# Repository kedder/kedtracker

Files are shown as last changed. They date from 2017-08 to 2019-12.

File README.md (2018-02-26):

# Ked Tracker - Open Glider Network tracker hardware

Based on design by glidernet.org project: http://wiki.glidernet.org/ogn-tracker-diy.

It is a small airborn avionic device that periodically transmits aircraft
position. Signal is picked up by ground-based receivers and published on Open
Glider Network, so that aircraft position can be found on  various aircraft
tracking systems, like http://glidertracker.de/ or
https://www.flightradar24.com/. It is also received by other OGN tracker
devices in the vicinity and can be used to improve pilot' situation awareness.
See http://wiki.glidernet.org/ for more information.

Ked Tracker is designed using [KiCad](http://kicad-pcb.org/) electronic schematic and PCB design software.

## Features

* Can be powered from onboard 12V power supply (or any 9-24V power
  supply for that matter).

* Standard NMEA output.

* Uses FLARM NMEA sentences to report detected nearby aircrafts for
  interoperability with existing hardware and software.

* Communication via standard IGC RJ45 socket.
  Allows to re-use existing equipment like FLARM viewers or cables.

* Communication via USB interface. Device is visible as virtual COM port
  when connected to a computer. Requires no special cables other then standerd
  micro-USB cable. Device can also be powered by 5V from USB interface.

* Communication via Bluetooth. For hassle-free wireless connection with
  phone or tablet.

* Barometric sensor onboard for more precise altitude measurement.

* Slot for SD-card. Currently for logging device activity. Firmware for IGC
  flight logger is pending.

* Beeper to provide sound feedback for important events.

## Schematics

Current schematics can be also downloaded in
[PDF format](hardware/render/kedtracker.pdf?raw=true).

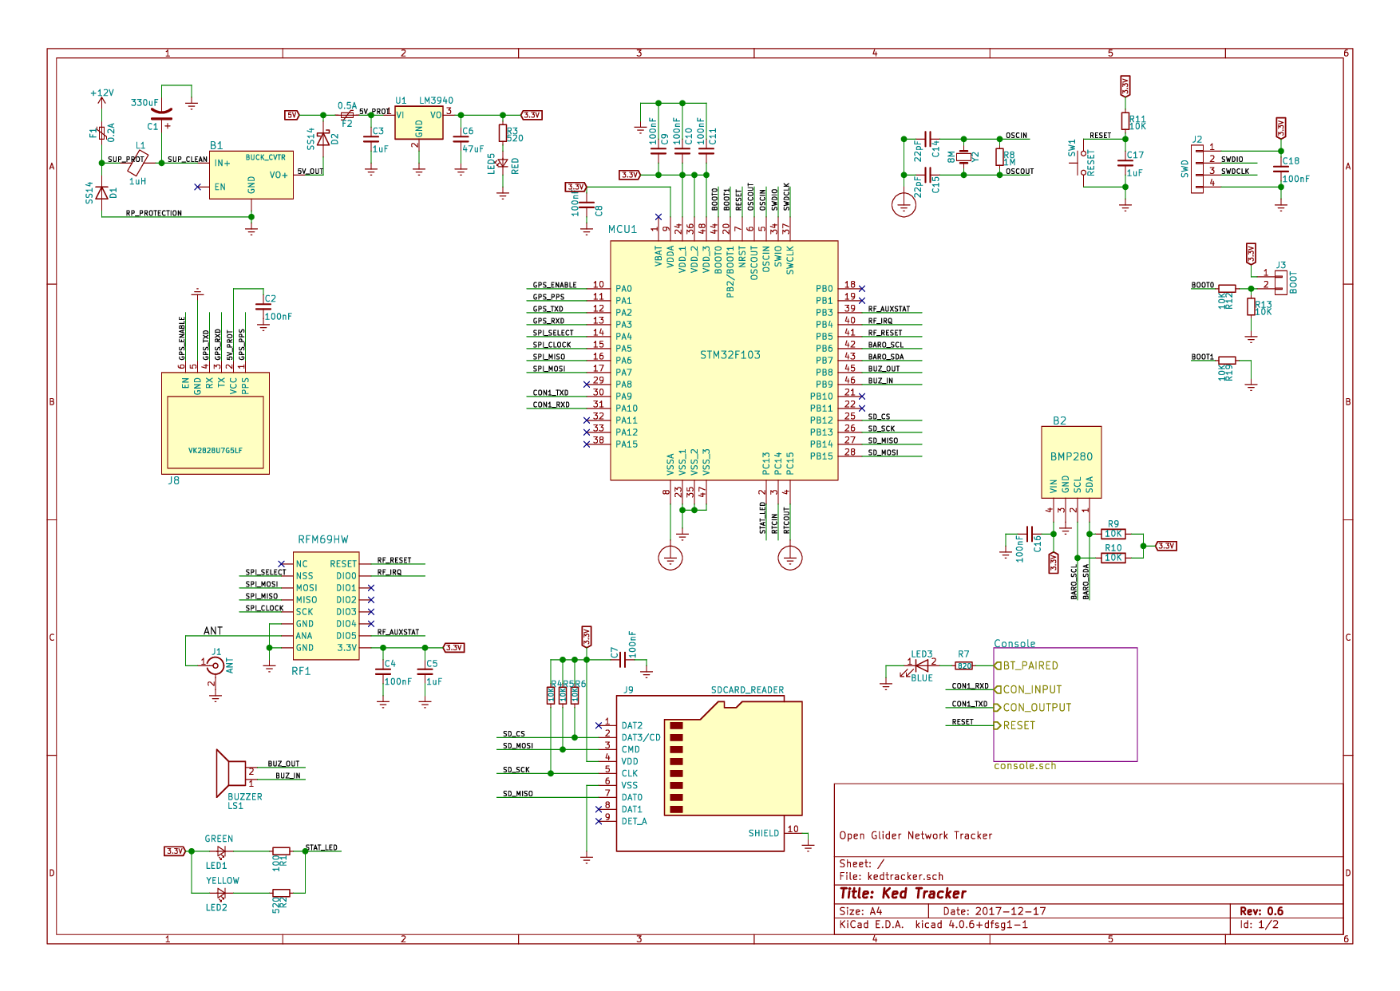
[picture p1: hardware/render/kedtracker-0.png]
Schematic Page 1

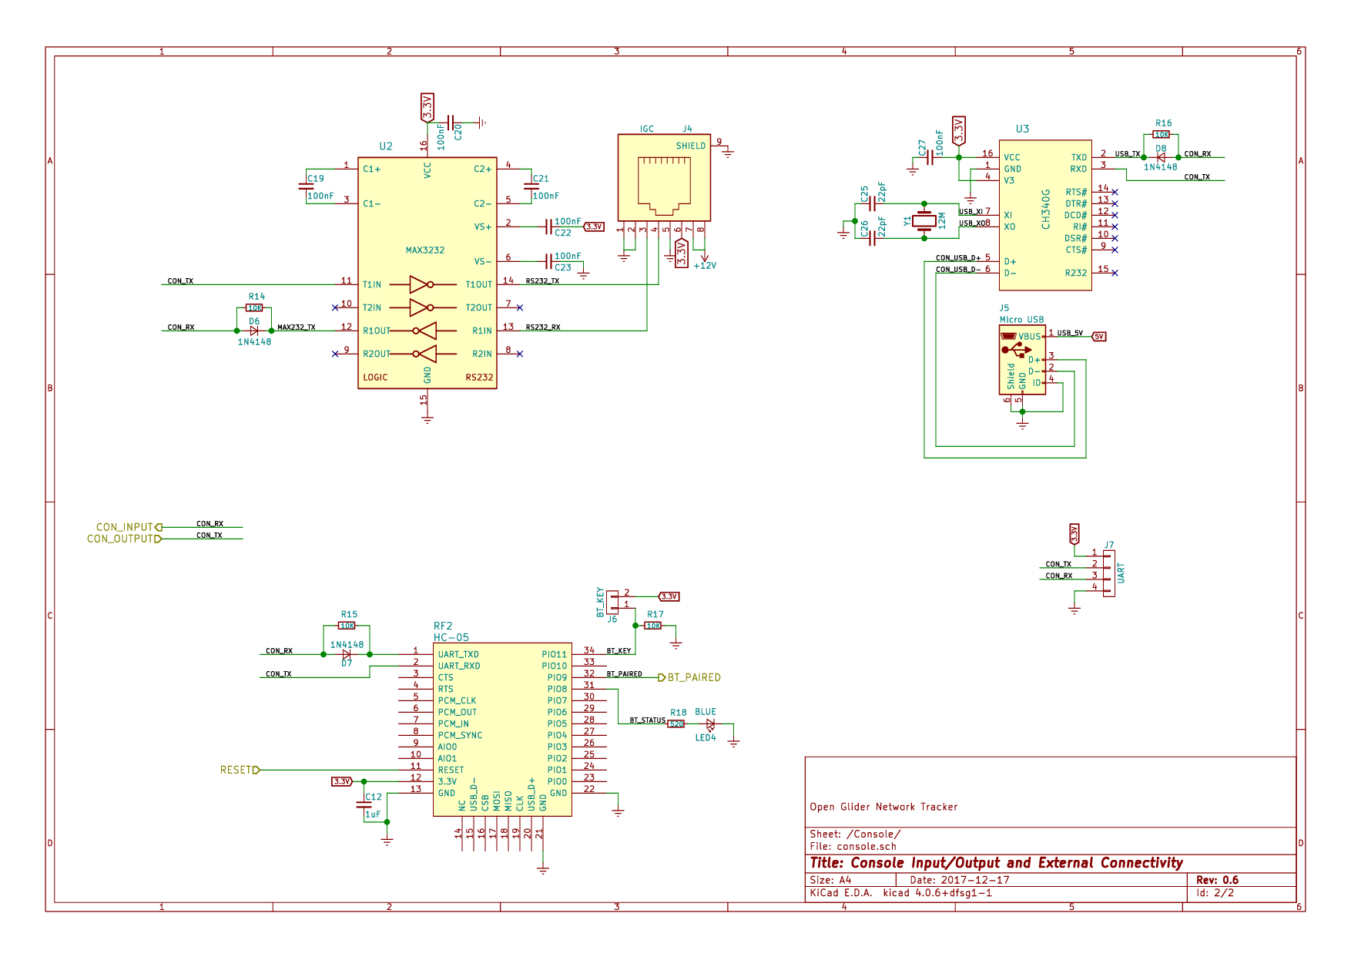
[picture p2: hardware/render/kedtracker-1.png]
Schematic Page 2


## Setting Up Development Environment

You will need to install additional packages for development. Packages for
ubuntu are specified here; other operating systems might have similar
requirements.

### Building Firmware and Flashing MCU

```
sudo apt install gcc-arm-none-eabi openocd picocom
sudo add-user `whoami` plugdev
sudo add-user `whoami` dialout
```

### Developing Hardware

```
sudo apt install kicad
```

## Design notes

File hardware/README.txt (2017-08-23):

OGN Tracker Hardware

Notes:

To create laser printer templates plot:

  Front Layer: Mirrored
  Bottom Layer: Non-mirrored

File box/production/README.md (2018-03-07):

# Labels for produced boxes

This directory is automatically populated with labels for enclosures.

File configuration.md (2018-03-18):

# Configuring

# Tracker settings

## Tracker
Tracker is configured using $POGNS NMEA sentence

```
$POGNS,ACFTT,ADDRT,ADDR,RFT,TXPW,FQCORR,
```

Where:

  * `ACFTT` -- [0..15] aircraft-type: 1=glider, 2=towa plane, 3=helicopter, ...
  * `ADDRT` -- [0..3] addr-type: 1=ICAO, 2=FLARM, 3=OGN
  * `ADDR` -- [HHHHHH] Address (ID): 6 hex digits, 24-bit
  * `RFT` -- [0..1] RFM69HW (up to +20dBm) or W (up to +13dBm)
  * `TXPW` -- [dBm] Tx power, from -10 to 20
  * `FQCORR` -- [Hz] Tx/Rx frequency correction

Examples:

Set high transmission power:
```
$POGNS,TxPower=20
```

## Bluetooth Dongles

### HC-05

HC-05 requires "Key" pin (34) to be brought high in order to enter "AT mode".
Once in at mode, open serial terminal on 38400 baud rate and execute these
commands (each command should end with `CR` `LF`:

```
    AT
    AT+VERSION?
    AT+NAME=Ked Tracker XXXXXX
    AT+UART=115200,0,0
```

Default PIN is `1234`.

### HC-06

HC-06 is by default configured to read on 9600 baud rate. Connect it to via
USB-TTL cable and issue the following commands (no CR or LF at the end):

```
    AT
    AT+VERSION
    AT+NAMEKEDBTX
    AT+BAUD8
```

Default PIN is `1234`.

### HC-10 Bluetooth LE

HC-06 is by default configured to read on 9600 baud rate. It accepts commands
with CR+LF endings. To configure, use these commands:

```
    AT+VERSION
    AT+NAMEKEDBTX
    AT+BAUD8
```

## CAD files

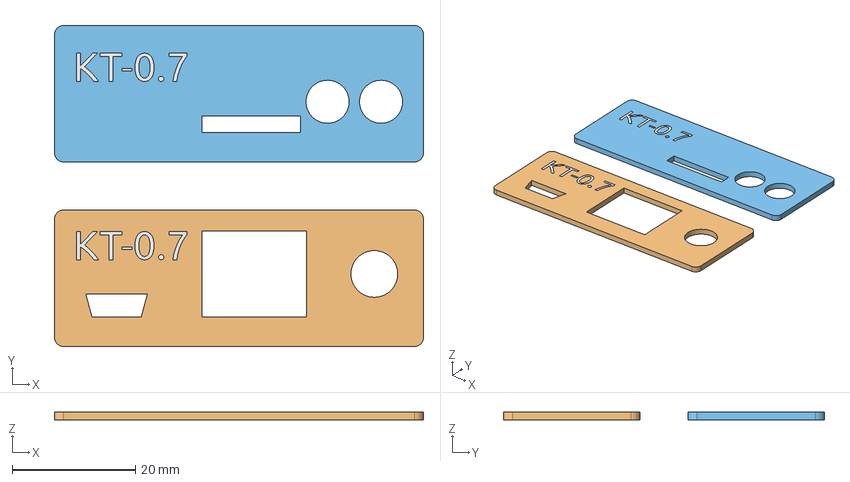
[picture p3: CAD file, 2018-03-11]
box/sideplates-0.7.fcstd
60.0 x 52.2 x 1.30 mm
Version-Front
Version-Back
Cut Back
Cut Front

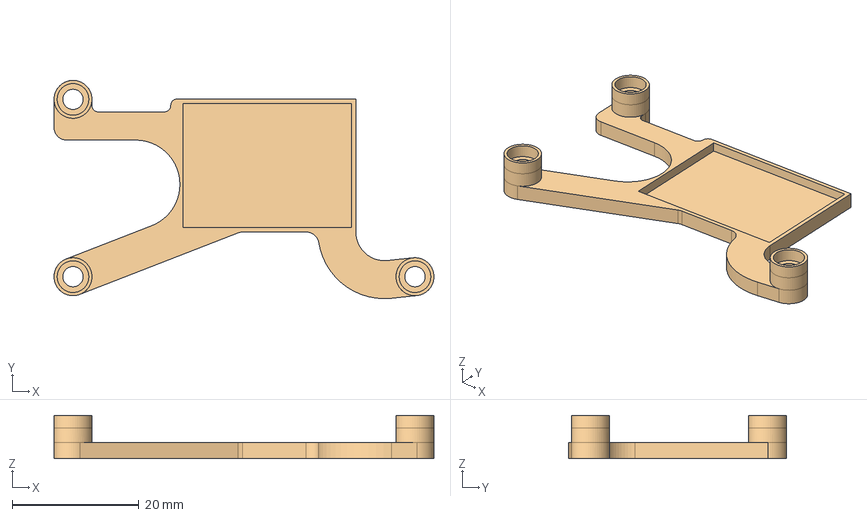
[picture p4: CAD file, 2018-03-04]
box/gpsframe2.fcstd
60.0 x 34.5 x 6.80 mm

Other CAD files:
box/sideplates-0.6.fcstd

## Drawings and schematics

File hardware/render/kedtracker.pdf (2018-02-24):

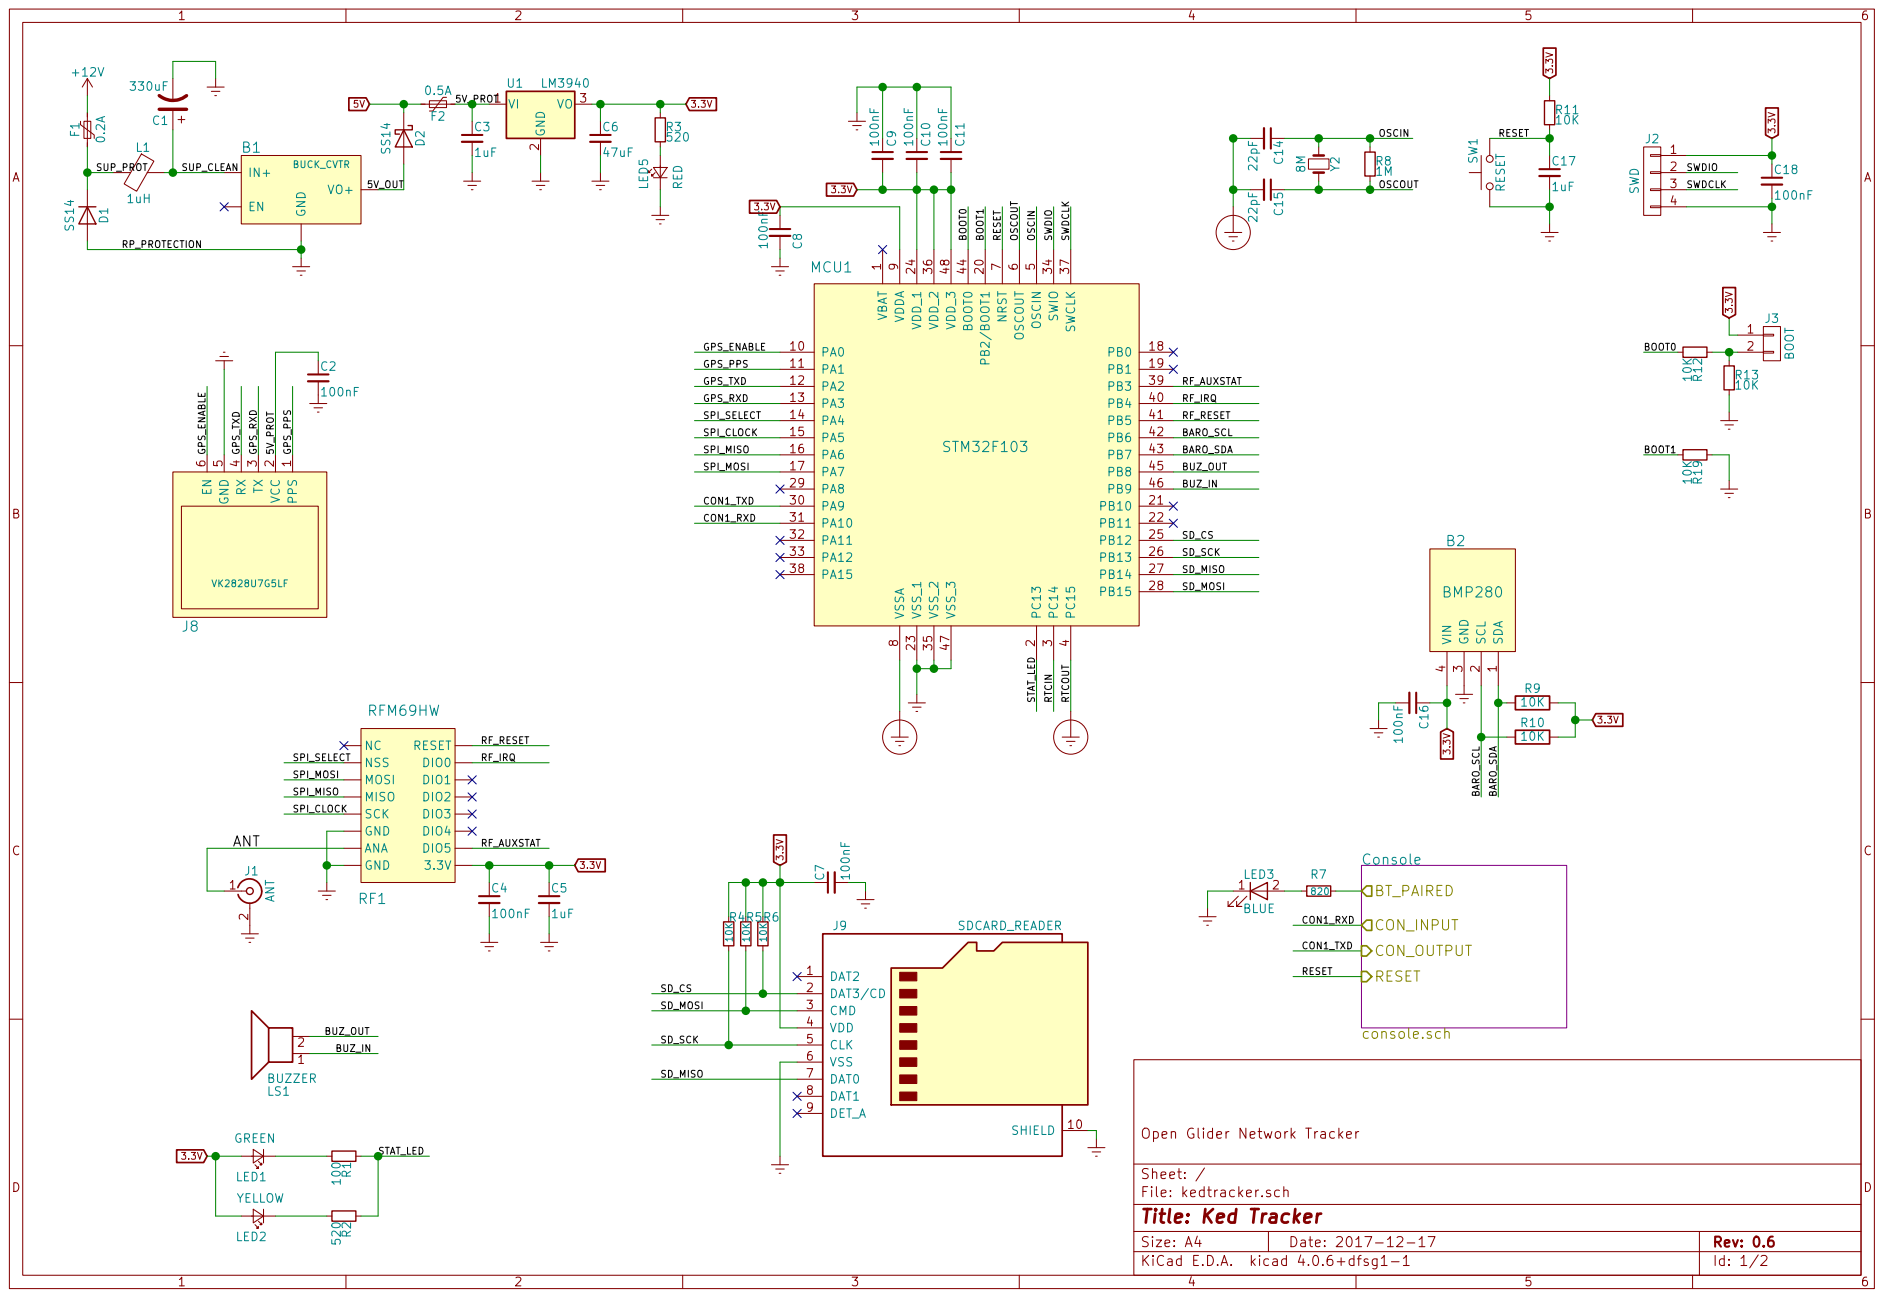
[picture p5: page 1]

SCK MISO MOSI NSS NC RF1RFM69HW

Id: 1/2 Title: Ked Tracker File: kedtracker.sch Sheet: / Open Glider Network Tracker 3.3V DIO5 DIO4 DIO3 DIO2 DIO1 DIO0 RESET GND

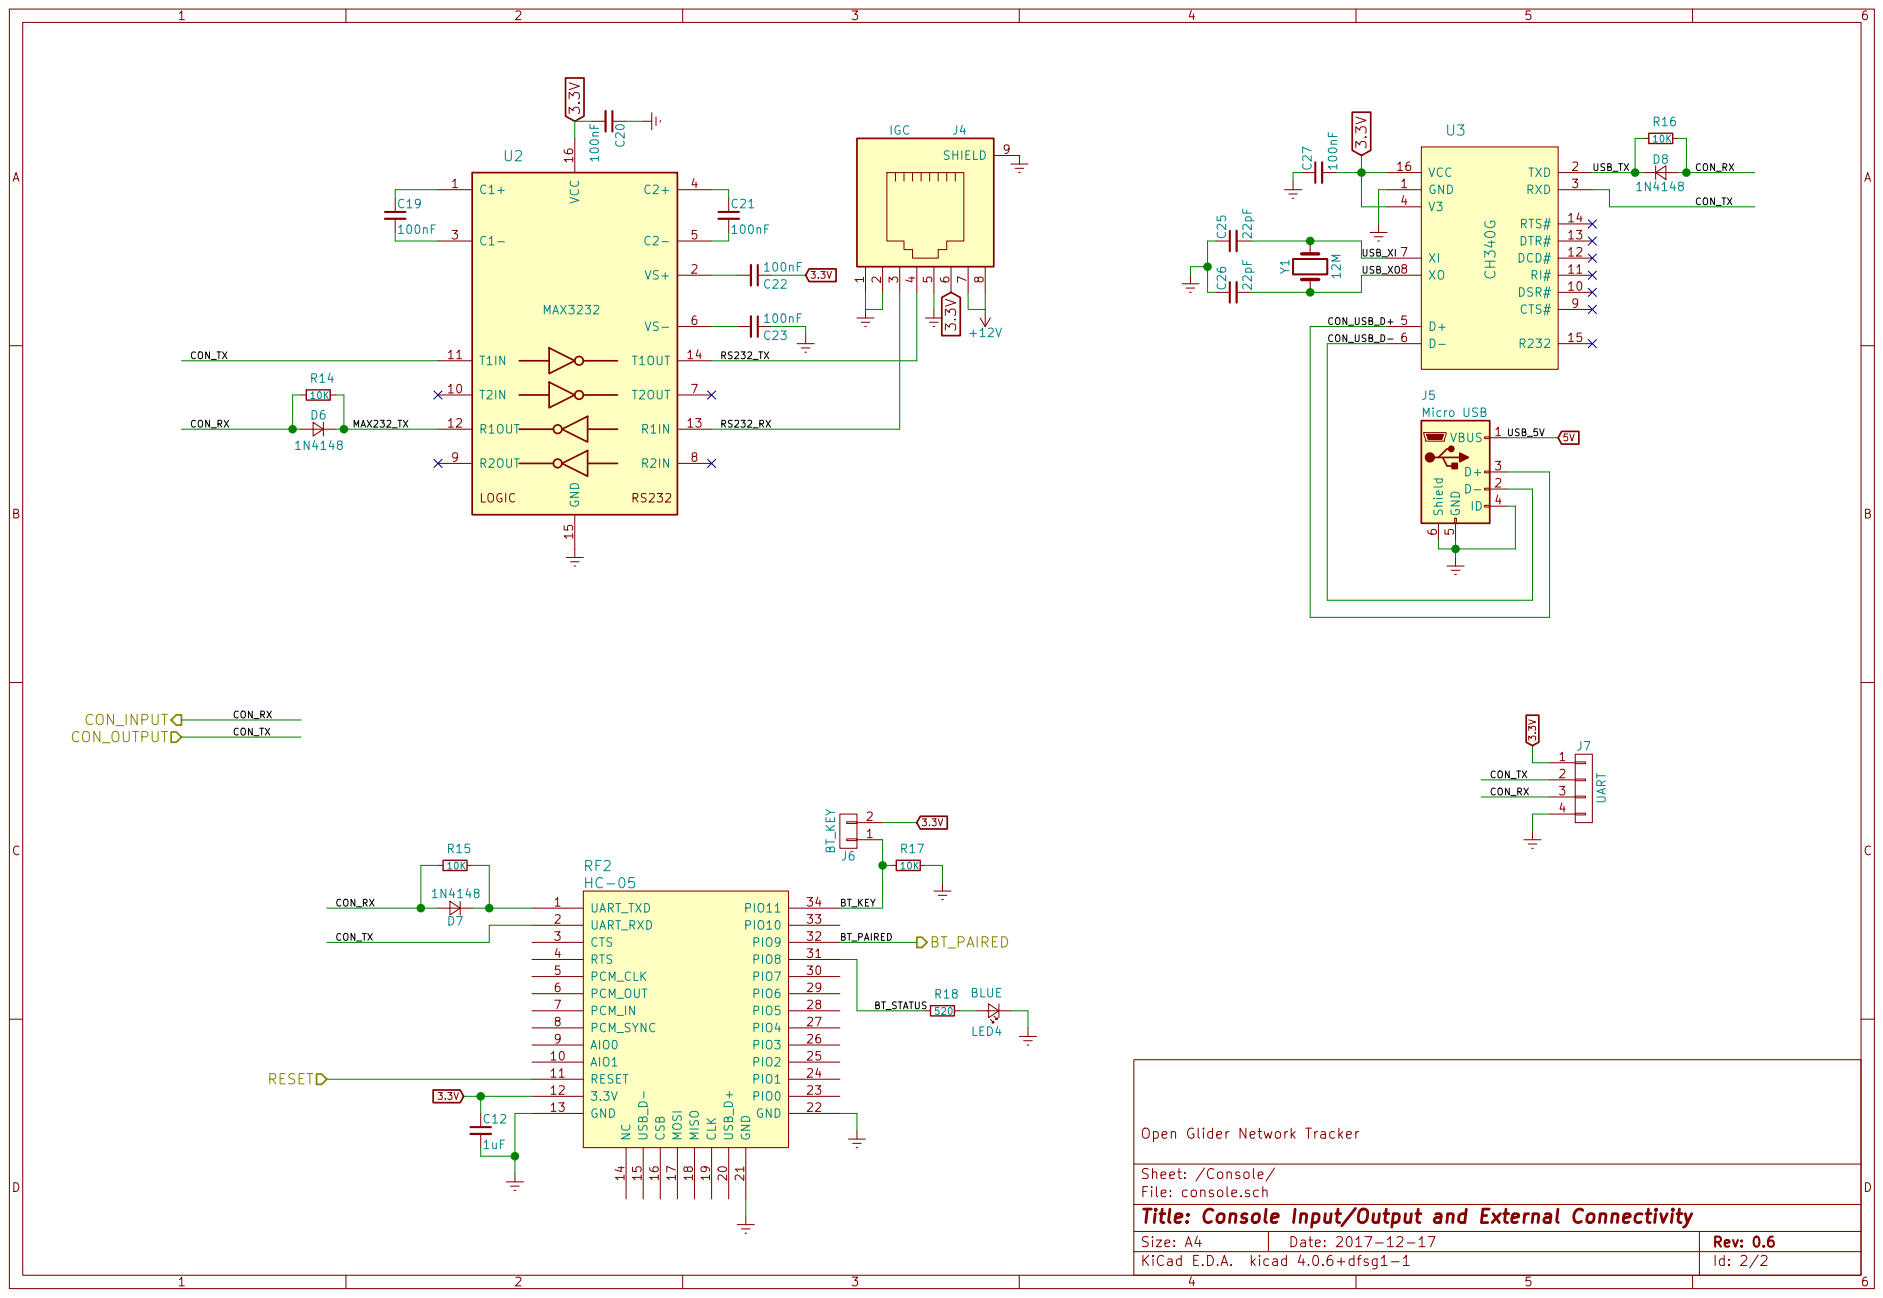
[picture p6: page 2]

File: console.sch Sheet: /Console/ Open Glider Network Tracker

Id: 2/2 Title: Console Input/Output and External Connectivity

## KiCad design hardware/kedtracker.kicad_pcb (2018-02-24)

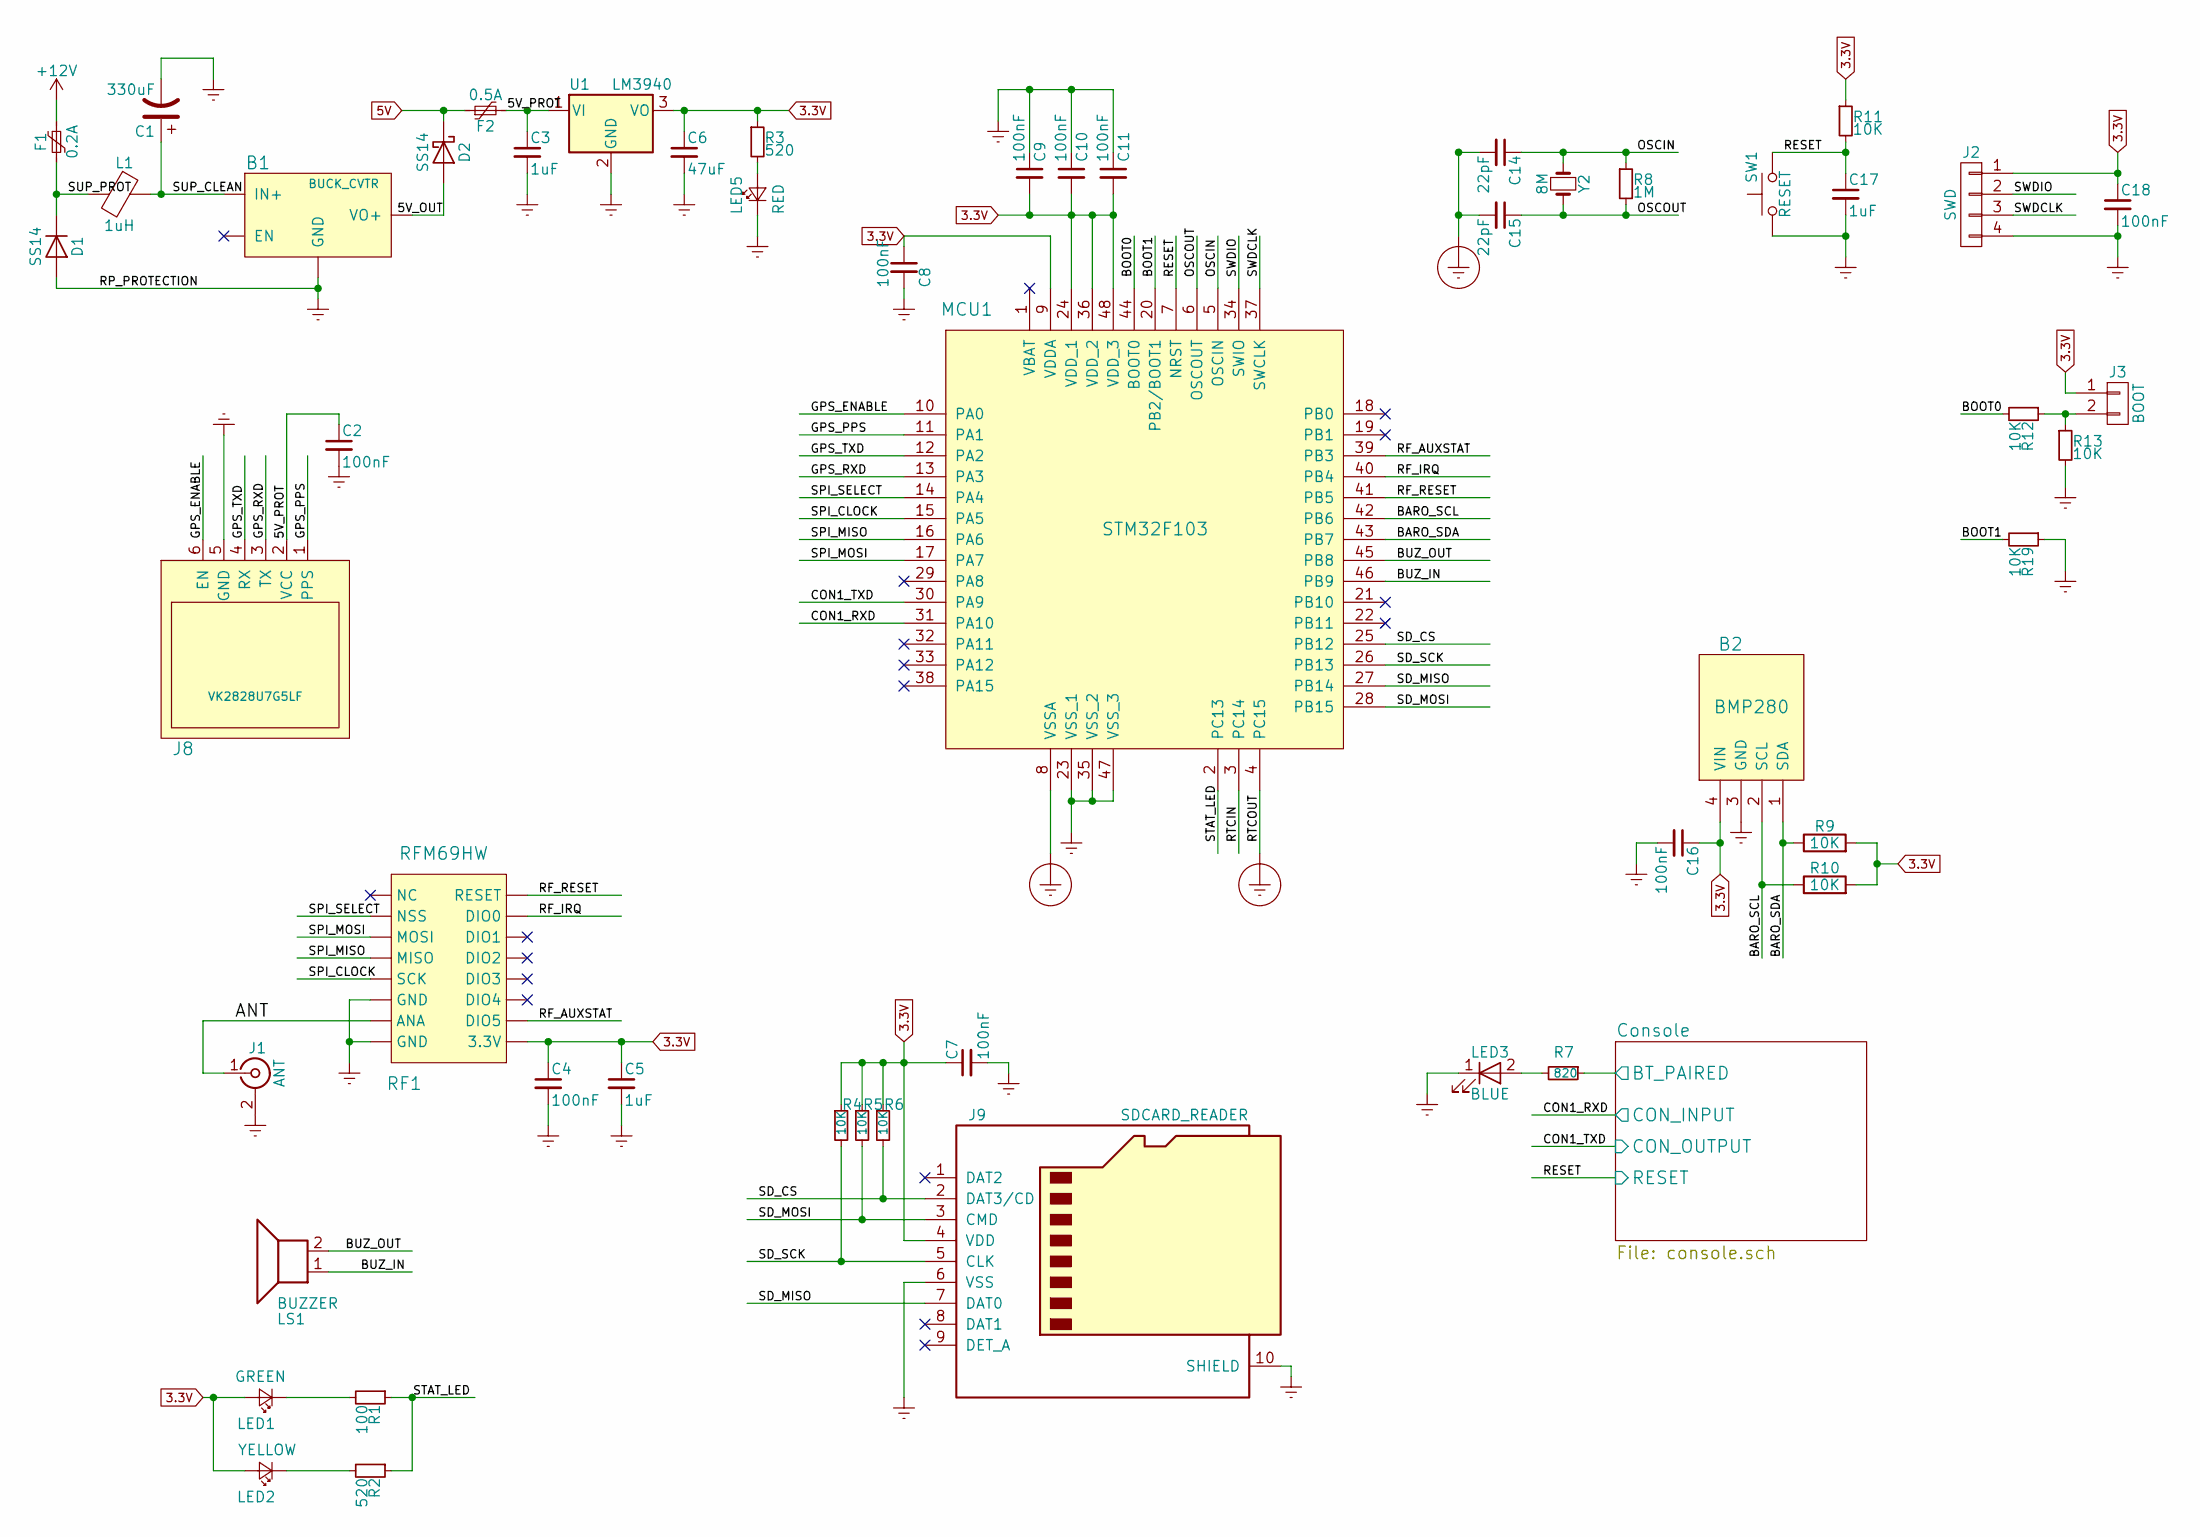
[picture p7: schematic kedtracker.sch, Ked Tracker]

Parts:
B1: BUCK_CVTR; Buck_Converter_Sm
B2: BMP280
C1: 330uF; CP_Radial_D6.3mm_P2.50mm
C2, C4, C7, C8, C9, C10, C11, C16, C18: 100nF; C_0805
C3, C5, C17: 1uF; C_1206
C6: 47uF; C_1210
C14, C15: 22pF; C_0603
D1, D2: SS14; D_SMA_Standard
F1: 0.2A; Fuse_SMD1206_Reflow
F2: 0.5A; Fuse_SMD1206_Reflow
J1: ANT; SMA_CONN
J2: SWD; Pin_Header_Straight_1x04_Pitch2.54mm
J3: BOOT; Pin_Header_Straight_2x01_Pitch2.54mm
J8: VK2828U7G5LF; Molex_PicoBlade_53047-0610_06x1.25mm_Straight
J9: SDCARD_READER; SDCARD_BOMB
L1: 1uH; INDUCTOR_V
LED1: GREEN; LED_D5.0mm_Horizontal_O3.81mm_Z3.0mm
LED2: YELLOW; LED_0603
LED3: BLUE; LED_D5.0mm_Horizontal_O3.81mm_Z3.0mm
LED5: RED; LED_0603
LS1: BUZZER; Buzzer_12x9.5RM7.6
MCU1: STM32F103; LQFP-48_7x7mm_Pitch0.5mm
R1: 100; R_0805
R2, R3: 520; R_0805
R4, R5, R6, R9, R10, R11, R12, R13, R19: 10K; R_0805
R7: 820; R_0805
R8: 1M; R_0805
RF1: RFM69HW
SW1: RESET; SW_SPST_SKQG
U1: LM3940; SOT-223-3Lead_TabPin2
Y2: 8M; Crystal_SMD_HC49-SD

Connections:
3.3V: B2.4 (VIN), C4.1, C5.1, C6.1, C7.1, C8.1, C9.2, C10.2, C11.2, C16.1, C18.1, J2.1, J3.1, J9.4 (VDD), LED1.2 (A), LED2.2 (A), MCU1.9 (VDDA), MCU1.24 (VDD_1), MCU1.36 (VDD_2), MCU1.48 (VDD_3), R3.1, R4.1, R5.1, R6.1, R9.2, R10.2, R11.1, RF1.1 (3.3V), U1.3 (VO); also elsewhere on the board
5V: D2.1 (K), F2.1; also elsewhere on the board
+12V: F1.1; also elsewhere on the board
/5V_OUT: B1.4 (VO+), D2.2 (A)
/5V_PROT: C2.1, C3.1, F2.2, J8.2 (VCC), U1.1 (VI)
/ANT: J1.1 (In), RF1.10 (ANA)
/BARO_SCL: B2.2 (SCL), MCU1.42 (PB6), R10.1
/BARO_SDA: B2.1 (SDA), MCU1.43 (PB7), R9.1
/BOOT0: MCU1.44 (BOOT0), R12.2
/BOOT1: MCU1.20 (PB2/BOOT1), R19.2
/BUZ_IN: LS1.1, MCU1.46 (PB9)
/BUZ_OUT: LS1.2, MCU1.45 (PB8)
/CON1_RXD: MCU1.31 (PA10); also elsewhere on the board
/CON1_TXD: MCU1.30 (PA9); also elsewhere on the board
/Console/BT_PAIRED: R7.1; also elsewhere on the board
/GPS_ENABLE: J8.6 (EN), MCU1.10 (PA0)
/GPS_PPS: J8.1 (PPS), MCU1.11 (PA1)
/GPS_RXD: J8.3 (TX), MCU1.13 (PA3)
/GPS_TXD: J8.4 (RX), MCU1.12 (PA2)
/OSCIN: C14.1, MCU1.5 (OSCIN), R8.1, Y2.1
/OSCOUT: C15.1, MCU1.6 (OSCOUT), R8.2, Y2.2
/RESET: C17.1, MCU1.7 (NRST), R11.2, SW1.2; also elsewhere on the board
/RF_AUXSTAT: MCU1.39 (PB3), RF1.2 (DIO5)
/RF_IRQ: MCU1.40 (PB4), RF1.7 (DIO0)
/RF_RESET: MCU1.41 (PB5), RF1.8 (RESET)
/SD_CS: J9.2 (DAT3/CD), MCU1.25 (PB12), R6.2
/SD_MISO: J9.7 (DAT0), MCU1.27 (PB14)
/SD_MOSI: J9.3 (CMD), MCU1.28 (PB15), R5.2
/SD_SCK: J9.5 (CLK), MCU1.26 (PB13), R4.2
/SPI_CLOCK: MCU1.15 (PA5), RF1.12 (SCK)
/SPI_MISO: MCU1.16 (PA6), RF1.13 (MISO)
/SPI_MOSI: MCU1.17 (PA7), RF1.14 (MOSI)
/SPI_SELECT: MCU1.14 (PA4), RF1.15 (NSS)
/STAT_LED: MCU1.2 (PC13), R1.1, R2.1
/SUP_CLEAN: B1.2 (IN+), C1.1, L1.1
/SUP_PROT: D1.1 (K), F1.2, L1.2
/SWDCLK: J2.3, MCU1.37 (SWCLK)
/SWDIO: J2.2, MCU1.34 (SWIO)
Earth: B1.3 (GND), B2.3 (GND), C1.2, C2.2, C3.2, C4.2, C5.2, C6.2, C7.2, C8.2, C9.1, C10.1, C11.1, C16.2, C17.2, C18.2, D1.2 (A), J1.2 (Ext), J2.4, J8.5 (GND), J9.6 (VSS), J9.10 (SHIELD), LED3.1 (K), LED5.1 (K), MCU1.23 (VSS_1), MCU1.35 (VSS_2), MCU1.47 (VSS_3), R13.2, R19.1, RF1.9 (GND), RF1.11 (GND), SW1.1, U1.2 (GND); also elsewhere on the board
Earth_Protective: C14.2, C15.2, MCU1.4 (PC15), MCU1.8 (VSSA)
unnamed: J3.2, R12.1, R13.1
unnamed: LED1.1 (K), R1.2
unnamed: LED2.1 (K), R2.2
unnamed: LED3.2 (A), R7.2
unnamed: LED5.2 (A), R3.2

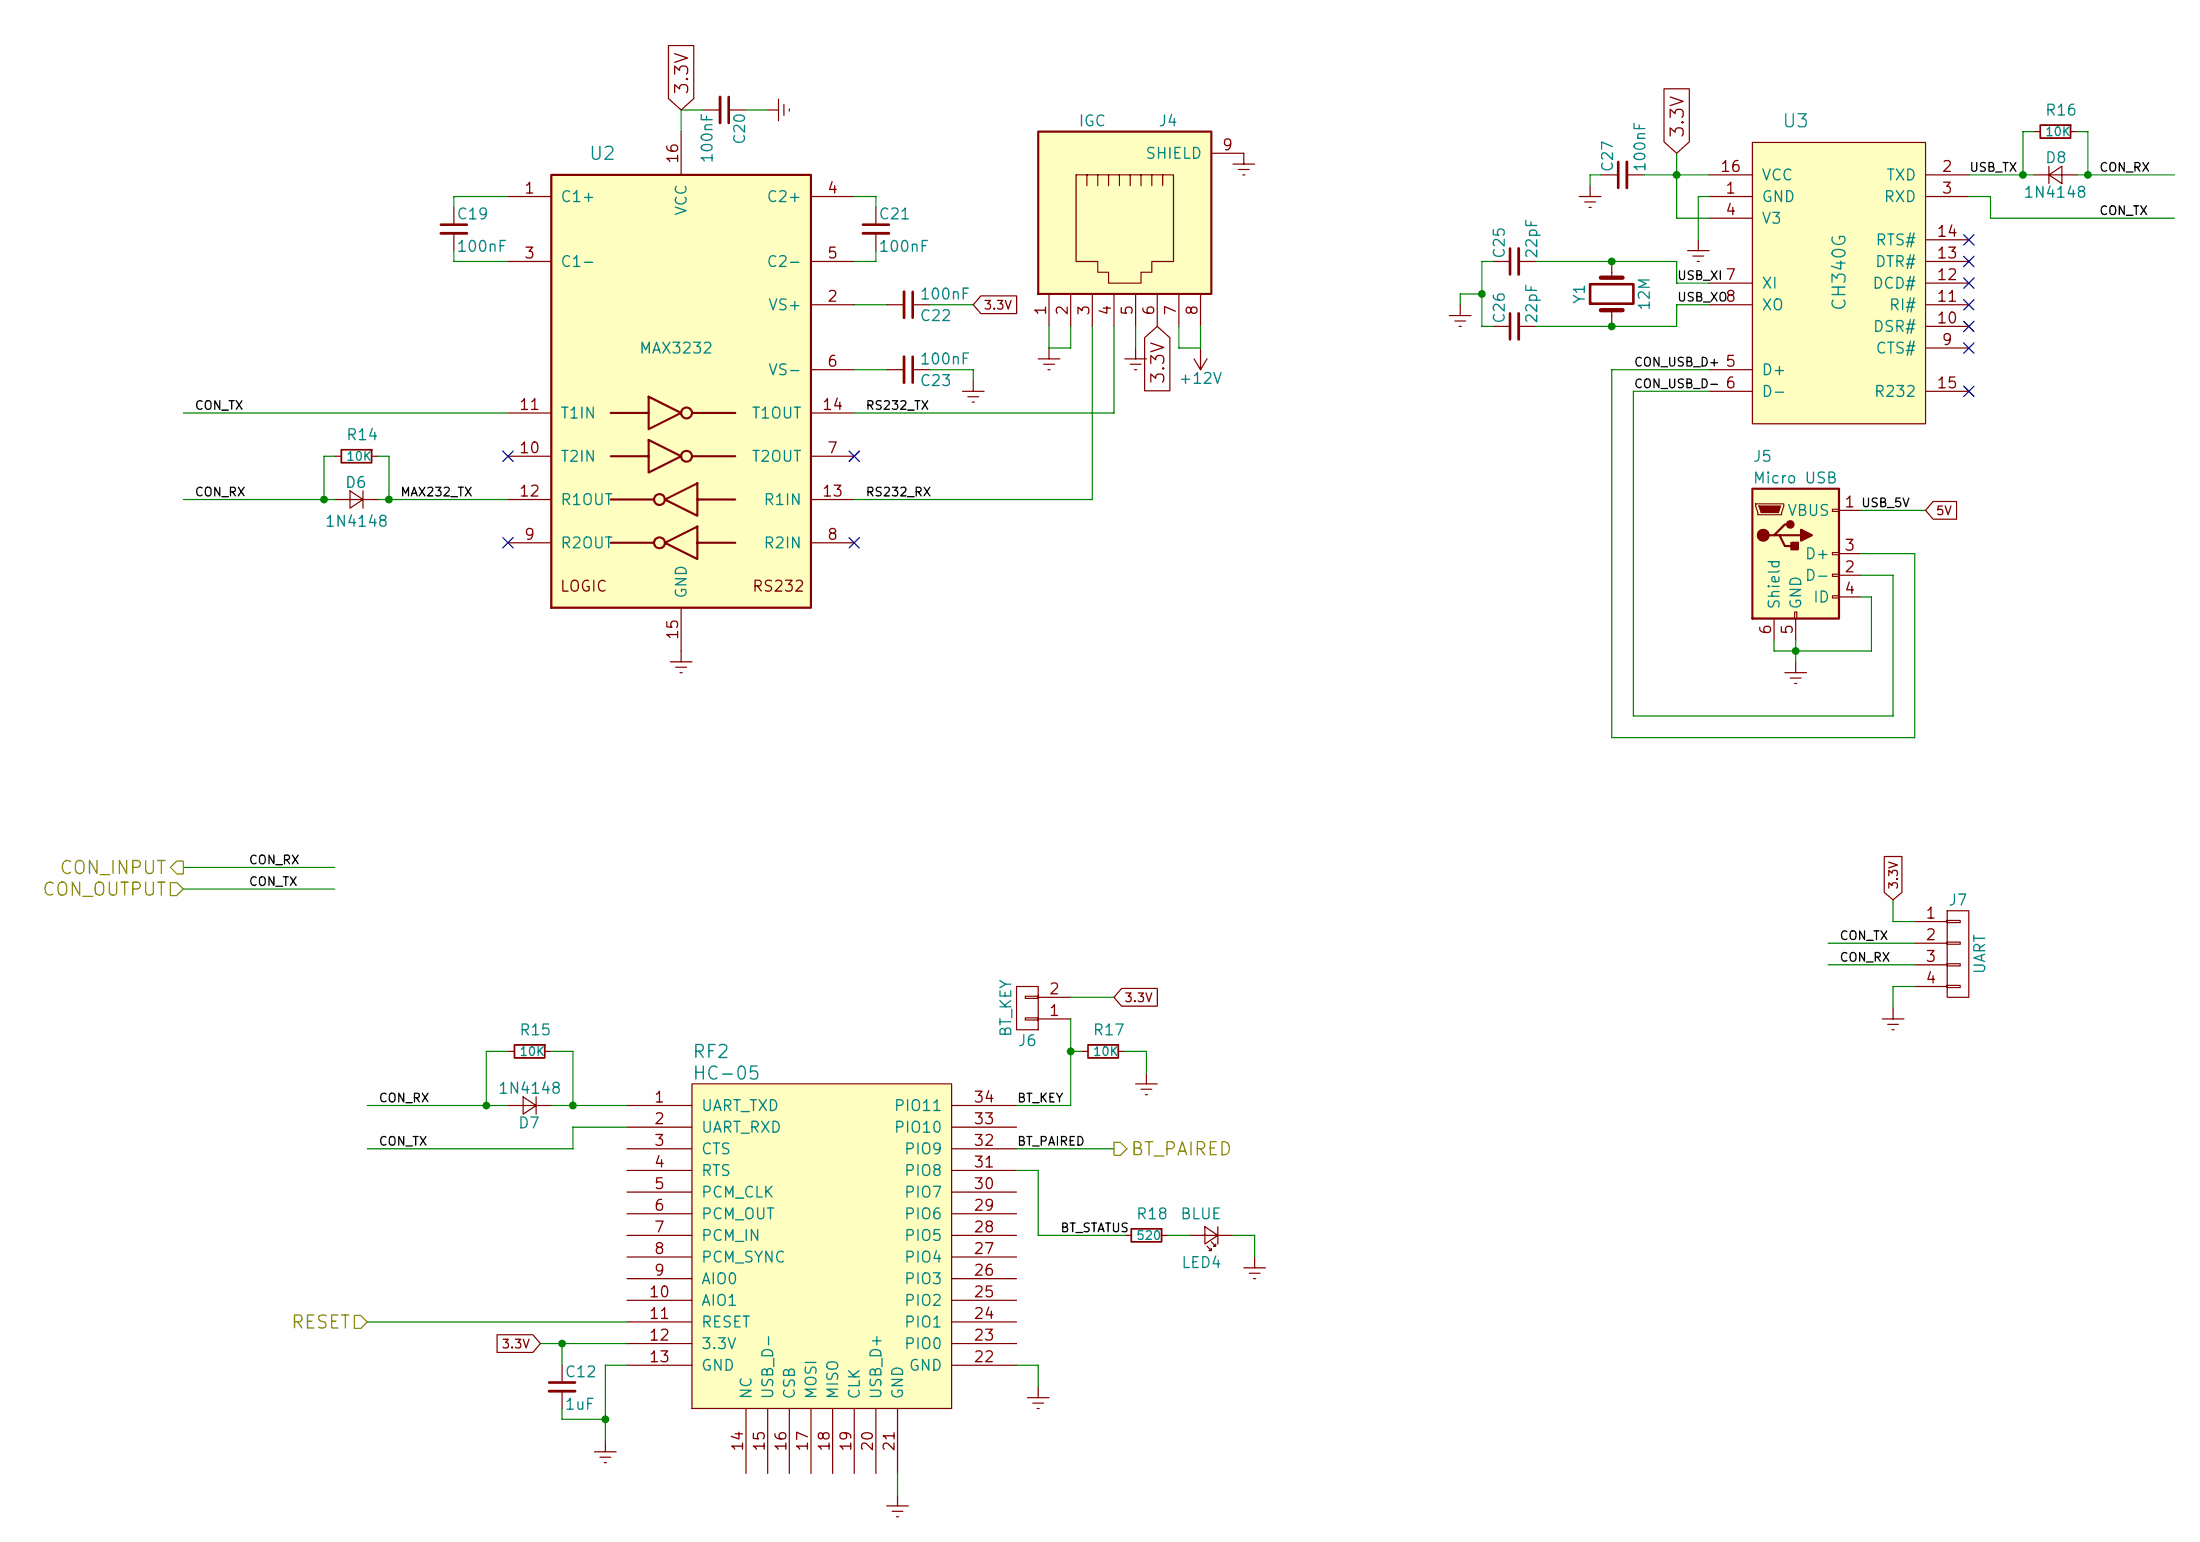
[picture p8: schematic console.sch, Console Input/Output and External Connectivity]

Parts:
C12: 1uF; C_1206
C19, C20, C21, C22, C23, C27: 100nF; C_0805
C25, C26: 22pF; C_0603
D6, D7, D8: 1N4148; D_1206
J4: IGC; RJ45_SOCKET_SHLD
J5: Micro USB; USB_Micro
J6: BT_KEY; Pin_Header_Straight_2x01_Pitch2.54mm
J7: UART; Pin_Header_Straight_1x04_Pitch2.54mm
LED4: BLUE; LED_0603
R14, R15, R16, R17: 10K; R_0805
R18: 520; R_0805
RF2: HC-05
U2: MAX3232; SOIC-16_3.9x9.9mm_Pitch1.27mm
U3: CH340G; SOIC-16_3.9x9.9mm_Pitch1.27mm
Y1: 12M; Crystal_HC49-4H_Vertical

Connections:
3.3V: C12.1, C20.2, C22.1, C27.2, J4.6, J6.2, J7.1, RF2.12 (3.3V), U2.16 (VCC), U3.4 (V3), U3.16 (VCC); also elsewhere on the board
5V: J5.1 (VBUS); also elsewhere on the board
+12V: J4.7, J4.8; also elsewhere on the board
/CON1_RXD: D6.2 (A), D7.2 (A), D8.2 (A), J7.3, R14.2, R15.2, R16.1; also elsewhere on the board
/CON1_TXD: J7.2, RF2.2 (UART_RXD), U2.11 (T1IN), U3.3 (RXD); also elsewhere on the board
/Console/BT_KEY: J6.1, R17.2, RF2.34 (PIO11)
/Console/BT_PAIRED: RF2.32 (PIO9); also elsewhere on the board
/Console/BT_STATUS: R18.2, RF2.31 (PIO8)
/Console/CON_USB_D+: J5.3 (D+), U3.5 (D+)
/Console/CON_USB_D-: J5.2 (D-), U3.6 (D-)
/Console/MAX232_TX: D6.1 (K), R14.1, U2.12 (R1OUT)
/Console/RS232_RX: J4.3, U2.13 (R1IN)
/Console/RS232_TX: J4.4, U2.14 (T1OUT)
/Console/USB_TX: D8.1 (K), R16.2, U3.2 (TXD)
/Console/USB_XI: C25.2, U3.7 (XI), Y1.2
/Console/USB_XO: C26.2, U3.8 (XO), Y1.1
/RESET: RF2.11 (RESET); also elsewhere on the board
Earth: C12.2, C20.1, C23.1, C25.1, C26.1, C27.1, J4.1, J4.2, J4.5, J4.9 (SHIELD), J5.4 (ID), J5.5 (GND), J5.6 (Shield), J7.4, LED4.1 (K), R17.1, RF2.13 (GND), RF2.21 (GND), RF2.22 (GND), U2.15 (GND), U3.1 (GND); also elsewhere on the board
unnamed: C19.1, U2.1 (C1+)
unnamed: C19.2, U2.3 (C1-)
unnamed: C21.1, U2.4 (C2+)
unnamed: C21.2, U2.5 (C2-)
unnamed: C22.2, U2.2 (VS+)
unnamed: C23.2, U2.6 (VS-)
unnamed: D7.1 (K), R15.1, RF2.1 (UART_TXD)
unnamed: LED4.2 (A), R18.1

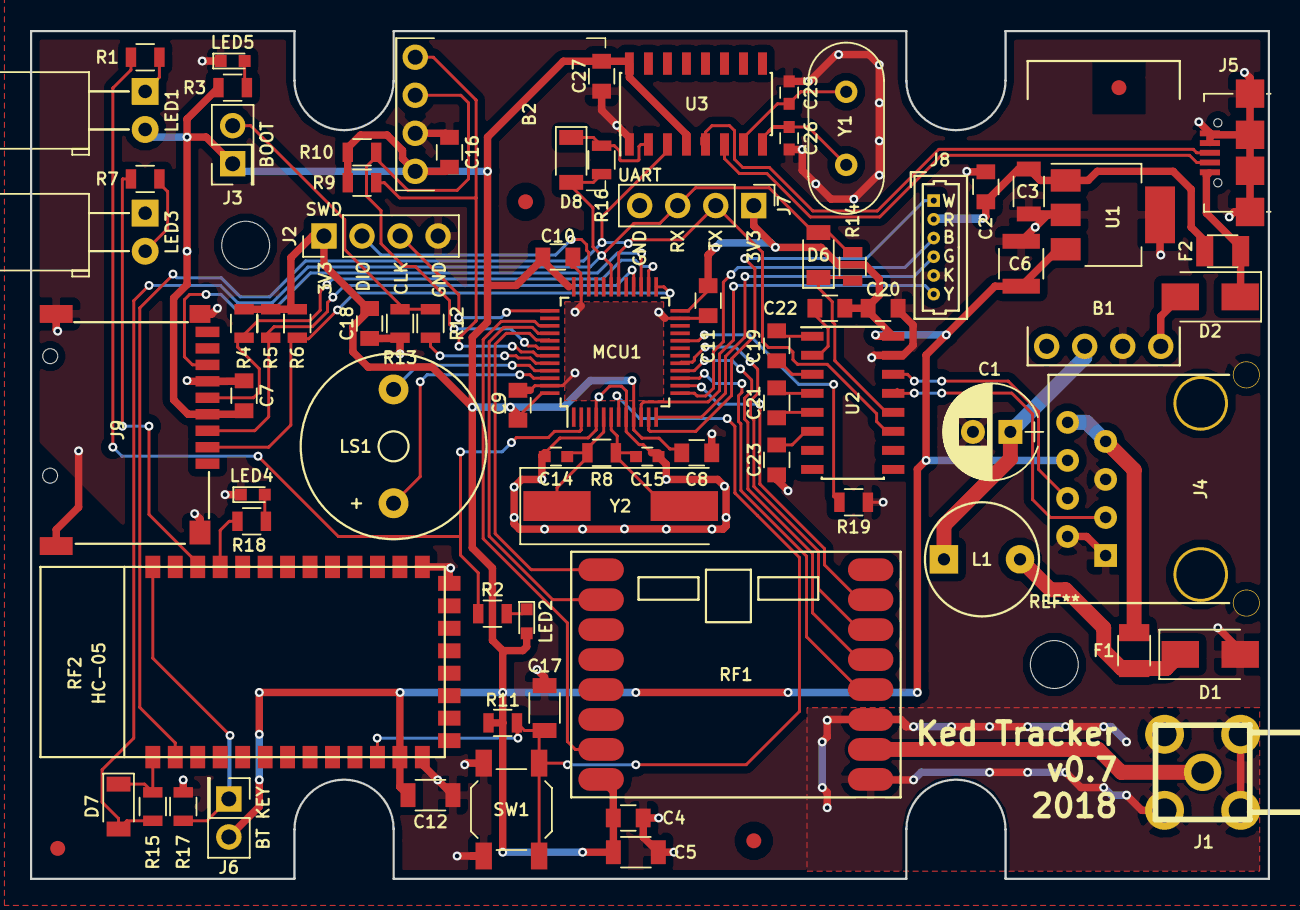
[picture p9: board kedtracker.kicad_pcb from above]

Board: 2 copper layers, 82.7 x 56.6 mm, 78 parts (0 on the bottom side), 63 nets.

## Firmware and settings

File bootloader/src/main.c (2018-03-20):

/*
 * Bootloader for STM32F103
 * Copyright (C) 2018 Andrey Lebedev
 *
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
 * You should have received a copy of the GNU General Public License
 * along with this program.  If not, see <http://www.gnu.org/licenses/>.
*/

#include <stdbool.h>

#include "stm32f10x.h"
#include "stm32f10x_flash.h"

#include "hal.h"
#include "ff.h"
#include "serial.h"
#include "crc32.h"
#include "firmware.h"

static FATFS FatFs;  // FatFS object for the file system (FAT)

typedef  void (*pFunction)(void);

static uint32_t  JumpAddress;
static pFunction Jump;
static void RunApp() {
  PrintLn("Starting application...");
//	    HAL_RCC_DeInit();
//	    HAL_DeInit();

  SysTick->CTRL = 0;
  SysTick->LOAD = 0;
  SysTick->VAL  = 0;

  JumpAddress = *(__IO uint32_t*)(MAIN_PROGRAM_START_ADDRESS + 4);
  Jump = (pFunction)JumpAddress;
  SCB->VTOR = MAIN_PROGRAM_START_ADDRESS;
  __set_MSP(*(__IO uint32_t*)MAIN_PROGRAM_START_ADDRESS);
  Jump();
  while (1) continue;
}

int main(void) {
  FRESULT ErrFile;

  HAL_SetupHardware();

  Print("** ");
  Print(BOOTLOADER_NAME);
  Print(" version ");
  Print(BOOTLOADER_VERSION);
  PrintLn(" **");
  Print("Installed application version: ");
  FW_PrintCurrentVersion();
  PrintLn("");

  ErrFile=f_mount(&FatFs, "", 1);
  if (ErrFile) {
    PrintLn("No SD Card.");
    RunApp();
    return 1;
  }

  static FoundFirmware found;
  FirmwareStatus fwstat = FW_FindFirmware(&found);
  if (fwstat != FW_FOUND) {
    RunApp();
    return 3;
  }

  FW_FlashFirmware(&found);

  PrintLn("Storing flashed version");
  FW_SaveHeader(&found.header);

  RunApp();
	return 0;
}

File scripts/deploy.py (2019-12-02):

import os
import time
import sys
import re
import subprocess

import serial
from termcolor import cprint, colored

PORT = '/dev/ttyUSB0'

APP_START_ADDR = '0x08002000'
APP_START_PAGE = '8'
BOOTLOADER_BUILD_DIR = 'bootloader/build'
APP_BUILD_DIR = 'firmware/build'
BOOTLOADER_BIN = os.path.join(BOOTLOADER_BUILD_DIR, 'bootloader.bin')
SETUP_BIN = os.path.join(APP_BUILD_DIR, 'setup.bin')
MAIN_BIN = os.path.join(APP_BUILD_DIR, 'main.bin')

FLASH_BOOTLOADER_CMD = ['stm32flash', '-w', BOOTLOADER_BIN, PORT]
FLASH_SETUP_CMD = ['stm32flash', '-w', SETUP_BIN, '-s', '8', PORT]
RUN_CMD = ['stm32flash', '-g', APP_START_ADDR, PORT]

FEATURE_NAMES = {
    'bootloader': 'Bootloader running',
    'flashing': 'Firmware flashing',
    'aircraftid': 'Aircraft Id',
    'setupdone': 'Setup Completed',
    'sdcard': 'SD Card',
    'txpower': 'TX Power Configured',
    'rf': 'RF Chip',
    'baro': 'Barometric Sensor',
    'gps': 'GPS',
    'flashsize': 'Flash Size'
}

FEATURE_MARKERS = {
    'bootloader': r'Ked Tracker Bootloader',
    'flashing': r'Flashing firmware',
    'aircraftid': r'Parameters initialized: \d:\d:([0-9A-F]{6})',
    'setupdone': r'Setup completed!',
    'sdcard': r'Config file TRACKER.CFG:',
    'txpower': r'RFM69HW/\+20dBm',
    'rf': r'TaskRF: (v24)',
    'baro': r'BMP280:  @76',
    'gps': r'\$GPGSA',
    'flashsize': r'TaskCTRL.*(64|128)kB'
}

class Failure(Exception):
    pass


def flash_bootloader():
    cprint("Flashing bootloader...", 'blue')

    res = subprocess.call(FLASH_BOOTLOADER_CMD)
    if res:
        raise Failure("Flashing bootloader failed!")


def flash_setup():
    cprint("Flashing setup firmware...", 'blue')
    res = subprocess.call(FLASH_SETUP_CMD)
    if res:
        raise Failure("Flashing setup firmware failed!")
    cprint("Starting setup firmware...", 'blue')
    res = subprocess.call(RUN_CMD)
    if res:
        raise Failure("Starting firmware failed!")


def detect_features():
    features = {}
    with serial.Serial(PORT, 115200, timeout=0) as ser:
        cprint('Detecting features...', 'blue')
        to_detect = set(FEATURE_MARKERS.keys())

        attempt = 50
        while attempt:
            try:
                line = ser.readline().decode()
            except UnicodeDecodeError:
                continue

            if not line:
                time.sleep(0.1)
                continue

            attempt -= 1
            print(">", colored(line.strip(), 'white'))
            for feature, marker in FEATURE_MARKERS.items():
                match = re.search(marker, line)
                if match:
                    if match.groups():
                        features[feature] = match.groups()
                    if feature in to_detect:
                        to_detect.remove(feature)
                    cprint("  Detected: %s" % FEATURE_NAMES[feature], 'green')

            if not to_detect:
                break
        else:
            for feature in to_detect:
                cprint('  Not Detected: %s' % FEATURE_NAMES[feature], 'red')
            raise Failure("Not all features detected")

    cprint("All features detected", 'blue')
    return features


def report_success(features):
    print()

    aircraft_id, = features['aircraftid']
    flash_size, = features['flashsize']

    print(colored('Flash Size: %skB' % flash_size, 'blue'))
    print(colored('Your aircraft Id:', 'blue'),
          colored(aircraft_id, 'green', attrs=['bold']))
    cprint("Success!", 'blue')

def welcome():
    cprint("Setting up Ked Tracker", 'blue')
    print(colored("Put jumpers on", 'blue'),
          colored('BOOT', 'blue', attrs=['bold']),
          colored('and', 'blue'),
          colored('BT_KEY', 'blue', attrs=['bold']),
          colored('and press', 'blue'),
          colored("Enter", attrs=['bold']),
          end='')
    input('')

def main():
    welcome()
    flash_bootloader()
    flash_setup()
    features = detect_features()
    report_success(features)

if __name__ == '__main__':
    try:
        main()
    except Failure as e:
        cprint("*** Error: %s" % e, 'red')
        sys.exit(1)

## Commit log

2017-08-23 Initial commit
    Allow to flash microcontroller using openocd
    [stm32f1.cfg]
2017-08-23 Hardware project added
    [ogntracker.kicad_pcb, ogntracker.sch]
2017-08-27 Improvements to make hand-made board easier to produce
    * Wider copper base for pins
    * Proper size of CPU board
    * Added console headers
    [ogntracker.kicad_pcb, ogntracker.sch]
2017-08-27 Larger vias and tracks for DIY production
    [ogntracker.kicad_pcb]
2017-08-27 Version 0.2.0, manufactured
    [ogntracker.kicad_pcb, ogntracker.sch]
2017-08-29 Allow on-board GDB debugging
    [stm32f1.cfg]
2017-09-01 MAX232 added and 2 RJ45 sockets for comms
    [ogntracker.sch]
2017-09-16 Hardware 0.3 released for manufacturing
    [ogntracker.kicad_pcb, ogntracker.sch]
2017-09-16 Show Hardware Schematics
2017-11-04 Gerbers for 0.3 hardware release
    [ogntracker-B.Cu.gbl, ogntracker-B.Mask.gbs, ogntracker-B.SilkS.gbo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]
2017-11-05 Various updates to schematics and experiments with layout for new box
    [ogntracker.kicad_pcb, ogntracker.sch]
2017-11-12 Routed prototype board for HAMMOND 1593N box
    [console.sch, ogntracker.kicad_pcb, ogntracker.sch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]
2017-11-25 STM32 dev-board based schematics
    [ogntracker.sch]
2017-11-25 Unfinished pcb layouts
    [console.sch, ogntracker.kicad_pcb, prototype.kicad_pcb]
2017-12-11 Unverified attempt on standalone STM32 chip
    [console.sch, ogntracker.kicad_pcb, ogntracker.sch]
2017-12-11 Correct status diode direction
    [ogntracker.sch]
2017-12-11 Schematics pdf updated
2017-12-11 All the used footprints moved to project directory
    [console.sch, ogntracker.sch]
2017-12-11 Simple drawings for box panels
    [panels.kicad_pcb]
2017-12-11 Label for 3rd device
2017-12-14 v0.6 routed
    [console.sch, ogntracker.kicad_pcb, ogntracker.sch]
2017-12-16 Labels and slight tweaks for 0.6
    [ogntracker.kicad_pcb]
2017-12-16 Components renamed to be more uniform
    [console.sch, ogntracker.kicad_pcb, ogntracker.sch]
2017-12-17 More tweaks for new box
    [ogntracker.kicad_pcb]
2017-12-17 Naming library properly
    [console.sch, kedtracker.kicad_pcb, kedtracker.sch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]
2017-12-17 Updating schematics for publishing
    [console.sch, kedtracker.sch]
2017-12-17 Updated schematics and README
2017-12-17 More tweaks before release
    [console.sch, kedtracker.kicad_pcb, kedtracker.sch]
2017-12-18 Final tweaks
    [kedtracker.kicad_pcb]
2017-12-18 Remove non-archived gerbers (added by accident)
    [ogntracker-B.Cu.gbl, ogntracker-B.Mask.gbs, ogntracker-B.SilkS.gbo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]
2018-01-13 Better placement for values on Fab layers
    [kedtracker.kicad_pcb]
2018-01-23 Sideplates and GPS support for Hammond 1593L enclosure
    [gpsframe2.fcstd, sideplates.fcstd]
2018-02-03 Prepare fabrication layer for assembly
    * Proper placement of labels on F.Fab layer
    * Element outlines
    * Correct values of used components
    * LED values indicate color, rather then function
    [console.sch, kedtracker.kicad_pcb, kedtracker.sch]
2018-02-04 Changes and fixes for 0.7
    * Different 4-pin reset button (because I have a lot of those)
    * Bluethooth "paired" and "status" leds swapped - dashboard
    led will show "paired" status and will not annoyingly blink all
    the time
    [console.sch, kedtracker.kicad_pcb, kedtracker.sch]
2018-02-04 Baro board turned 90 degrees to fit into the board
    [kedtracker.kicad_pcb]
2018-02-14 Updates for power supply and reset button
    [console.sch, kedtracker.kicad_pcb, kedtracker.sch]
2018-02-16 Reset button resets bluetooth chip as well
    [console.sch, kedtracker.kicad_pcb]
2018-02-18 Preparing release 0.7
    [kedtracker.kicad_pcb, kedtracker.sch]
2018-02-19 Correct capacitor size
    [console.sch]
2018-02-24 Schematics updated to 0.7
    [console.sch, kedtracker.kicad_pcb, kedtracker.sch]
2018-02-24 Gerbers for 0.7 accepted for manufacturing
2018-03-04 Unbreak gps frame model
    [gpsframe2.fcstd]
2018-03-04 Box models for 0.6 and 0.7
    [gpsframe2.fcstd, sideplates-0.6.fcstd, sideplates-0.7.fcstd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]
2018-03-07 Boxes for 0.6 and 0.7 ready for mass production
    [sideplates-0.6.fcstd, sideplates-0.7.fcstd]
2018-03-07 Label generator and labels for recent versions
    [prodlist.csv]
2018-03-11 Thinner plates to accomodate the thickness of labels
    [sideplates-0.6.fcstd, sideplates-0.7.fcstd]
2018-03-18 Bootloader - initial version
    [stm32f1.cfg]
2018-03-18 Correct TX power configuration note
2018-03-22 Simple manual page added
    [prodlist.csv]
2019-12-02 Specify addresses explicitly until binutils-arm-none-eabi-2.33
2019-12-02 Update schematics to latest KiCAD version
    [console.sch, kedtracker.sch]

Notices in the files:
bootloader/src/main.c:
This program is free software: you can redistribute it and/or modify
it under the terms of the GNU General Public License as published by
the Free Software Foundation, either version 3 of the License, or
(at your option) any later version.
